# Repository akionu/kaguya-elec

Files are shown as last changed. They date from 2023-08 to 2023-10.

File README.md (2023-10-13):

# kaguya-elec

CanSatのための小型電装基板です。第19回能代宇宙イベント出場機体『かぐや』（同志社大学）のために作りました。

kiban

- 大幅な小型化を実現しました（当団体比）。42x25mmでここまでできる！
- 安定して動作しています。
- 50mから自由落下しても故障しませんでした（投下1回目）。

ブロック図：
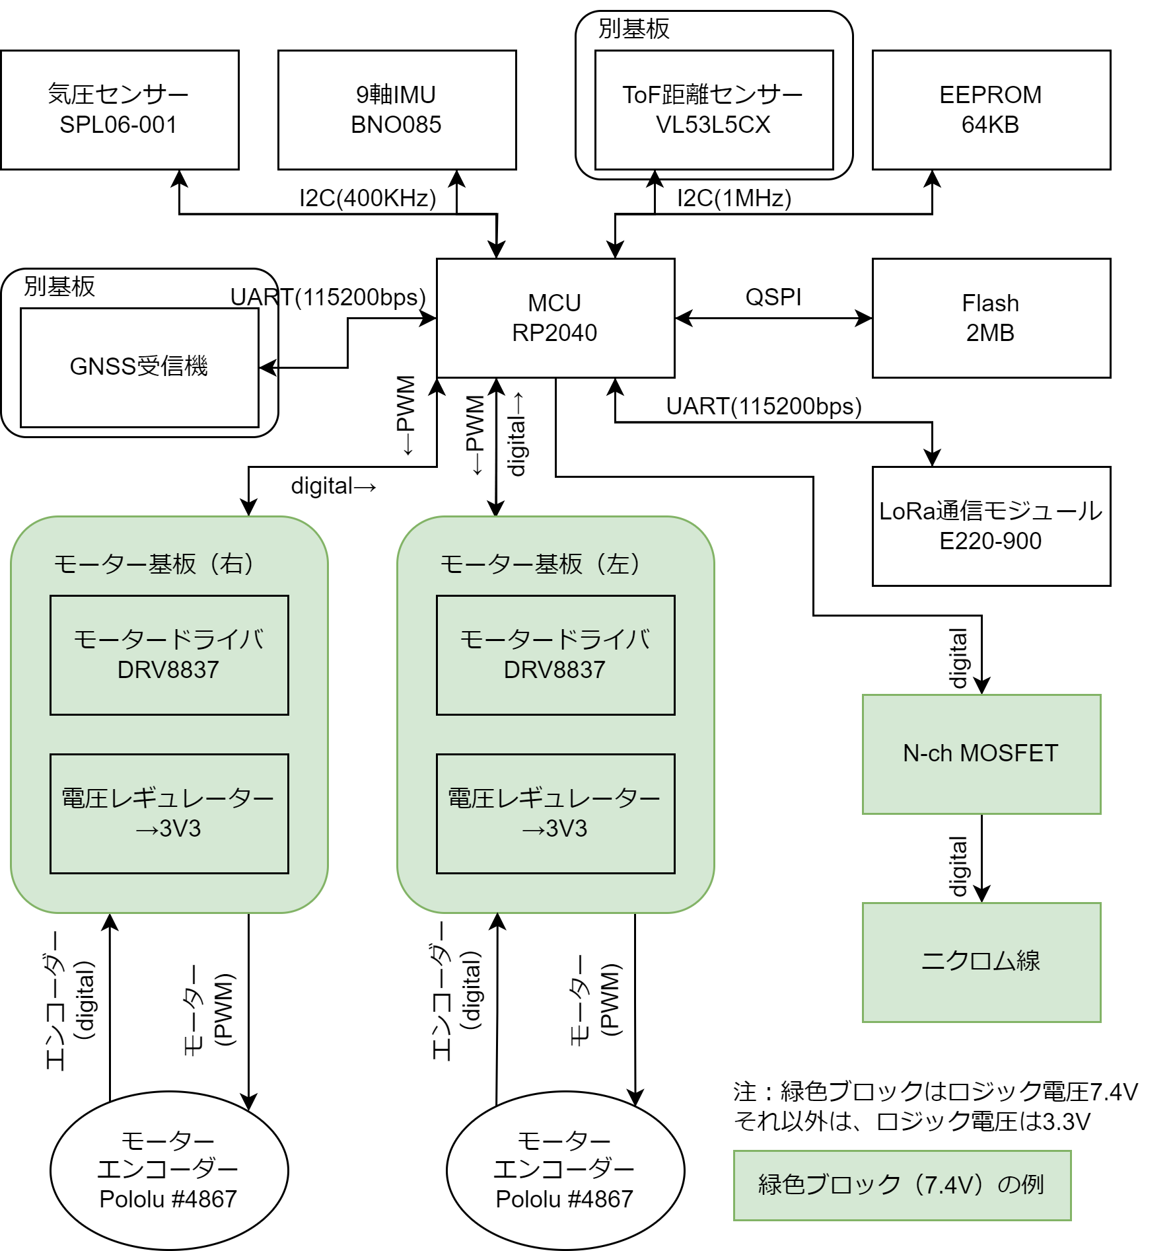
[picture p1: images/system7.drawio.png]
block_diagram

中身としては、RP2040を中心に、電源(DCDC)、無線（LoRa）、センサー（9軸IMU・気圧）、外付けセンサー用コネクタ（GPS・ToF測距）といった感じです。なお、モータードライバは別の基板として分離して使うようにしてあります。

回路図（詳しくはKiCadのデータを参照）：
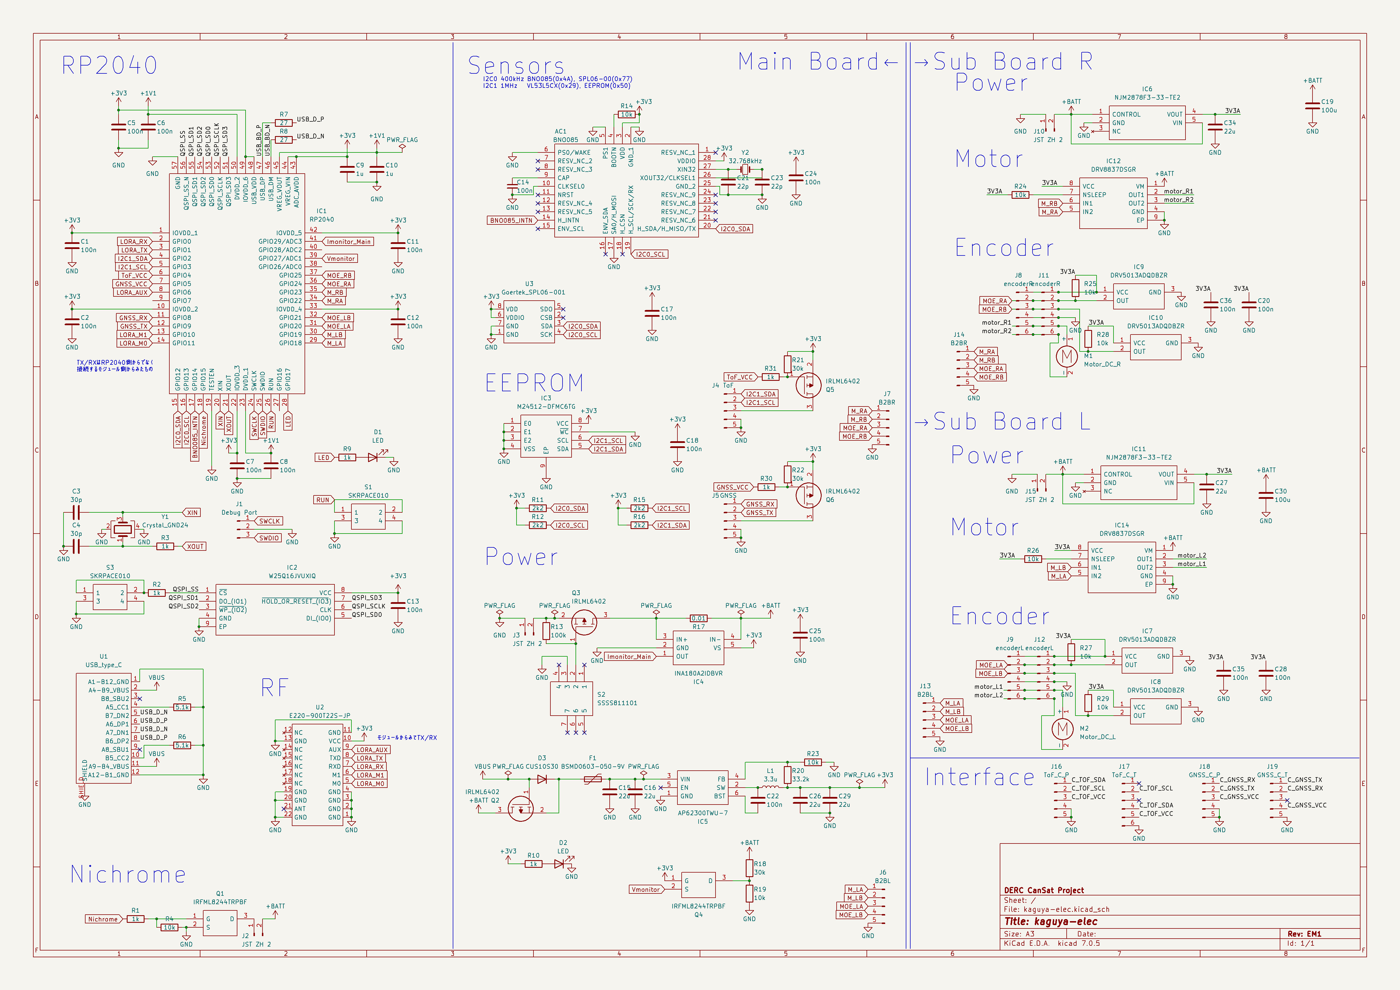
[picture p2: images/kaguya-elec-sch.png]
schematic


アートワーク：
表：
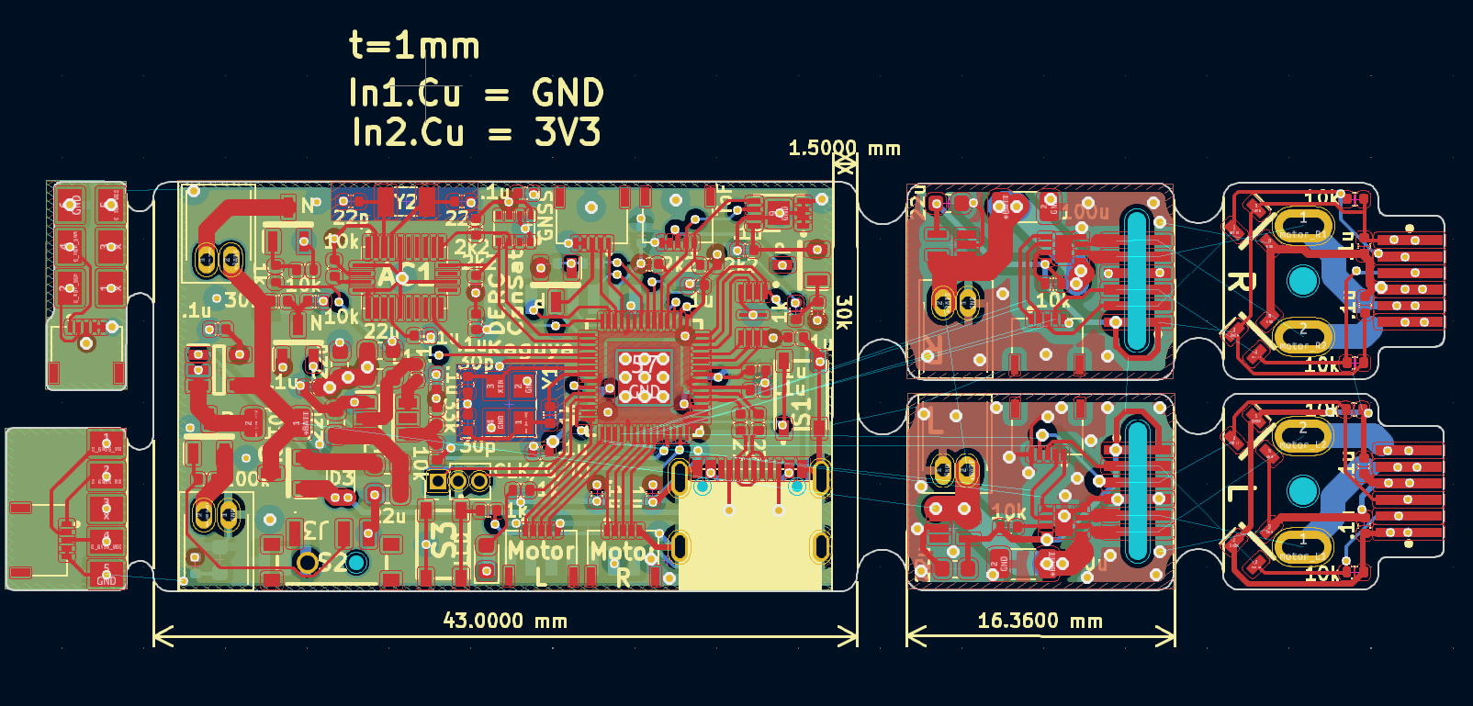
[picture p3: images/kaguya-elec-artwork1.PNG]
pcb_front

裏：
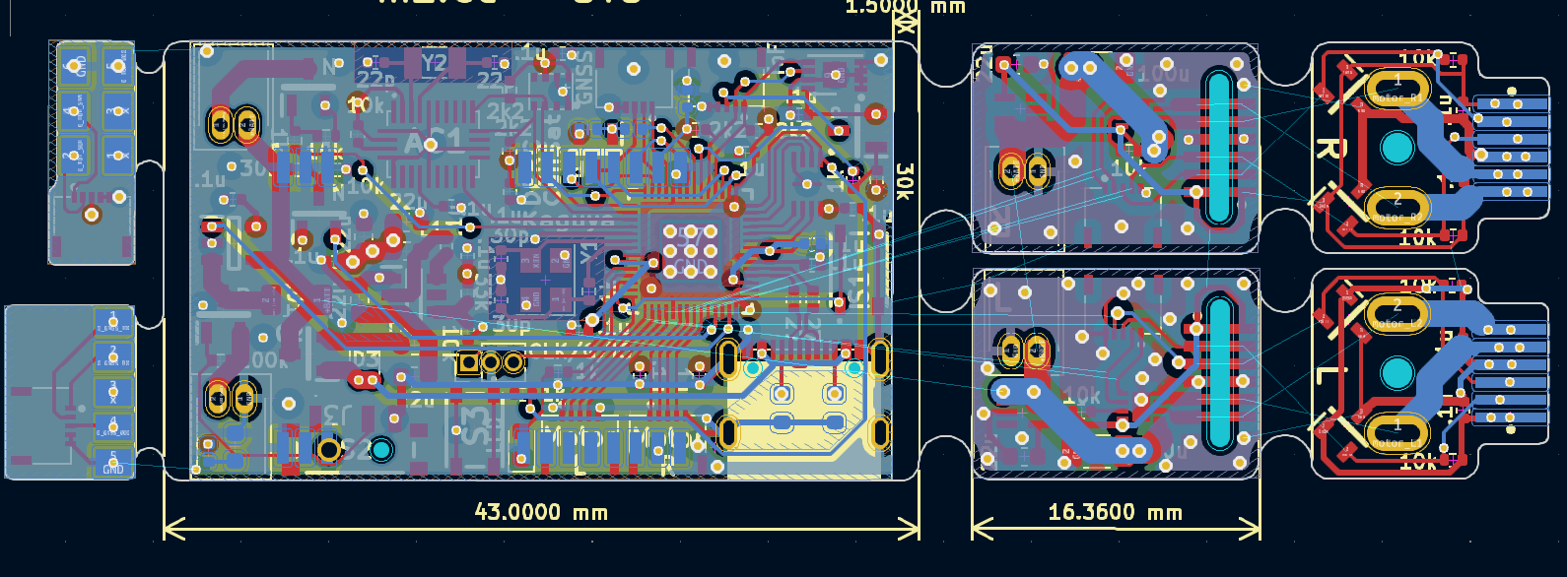
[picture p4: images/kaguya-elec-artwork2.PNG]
pcb_back


## 『かぐや』について

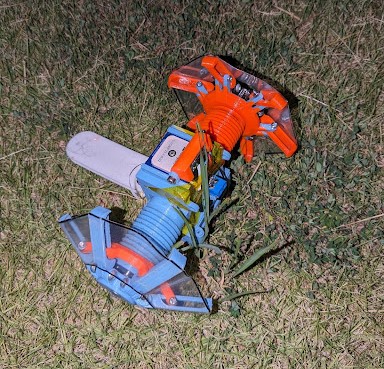
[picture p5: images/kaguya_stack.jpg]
kaguya_stack


第19回能代宇宙イベント出場機体『かぐや』（同志社大学）の基板です。
この機体の特徴：
- 成功率向上のため、2機体投下
    - タテに二つ重ねて投下するのでなく、制御性向上のため、ヨコに2つ並べてキャリアに収納
    - そのためのタイヤ展開
- 小型の基板

3回投下した中で、投下2回目の7mが最良の結果でした。実際の状況は大会報告書を参照されたいですが、走破性の不足によるスタックが一番の問題でした（3回ともプログラムは正常に動作・ログ取得）。
- 機体：運営特別賞
- ポスター：能代ロケット実験場　所長賞

なお、この基板で動かしたコードもGitHub上で公開しています。
[リンク](https://github.com/Yudetamago-AM/kaguya-code)

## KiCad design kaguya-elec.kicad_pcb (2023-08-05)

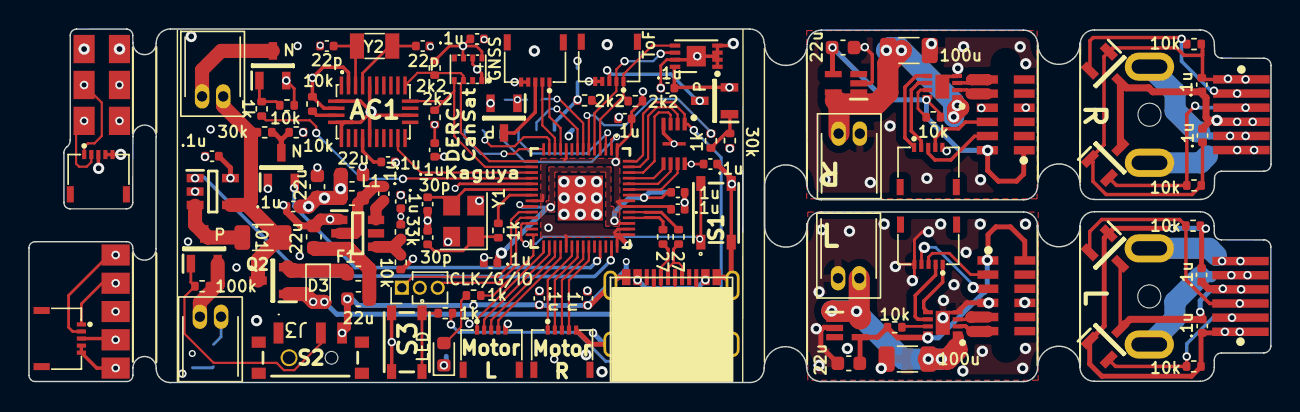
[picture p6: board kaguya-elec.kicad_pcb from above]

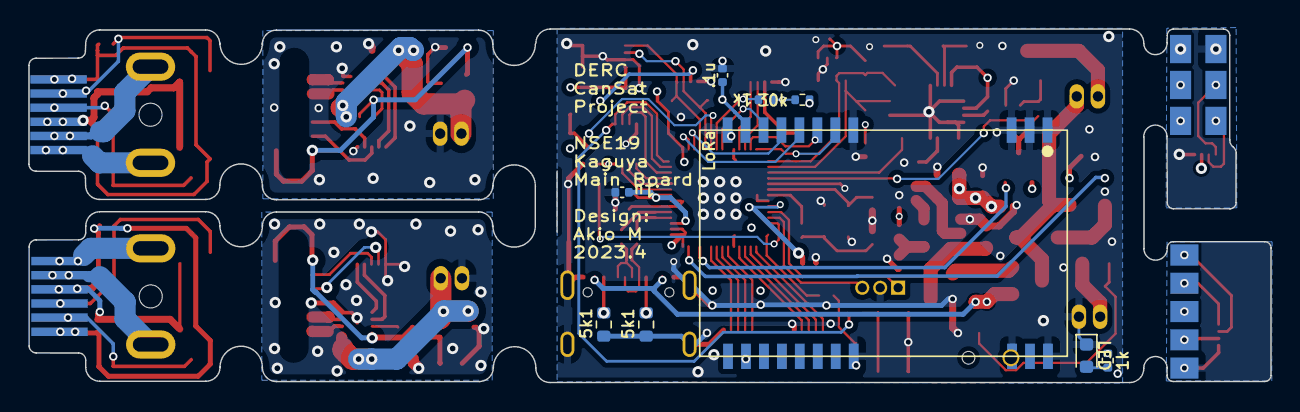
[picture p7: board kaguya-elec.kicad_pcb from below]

Board: 4 copper layers, 87.9 x 25.0 mm, 118 parts (9 on the bottom side), 84 nets.

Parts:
AC1: BNO085
C1, C2, C5, C6, C7, C8, C11, C12, C13, C14, C17, C18, C20, C22, C24, C25, C28, C35, C36: 100n; C_0402_1005Metric
C3, C4: 30p; C_0402_1005Metric
C9, C10: 1u; C_0402_1005Metric
C15, C16, C26, C27, C29, C34: 22u; C_0603_1608Metric
C19, C30: 100u; C_1206_3216Metric
C21, C23: 22p; C_0402_1005Metric
D1, D2: LED; LED_0603_1608Metric
D3: CUS10S30; D_SOD-323
F1: BSMD0603-050-9V; Fuse_0603_1608Metric
IC1: RP2040; RP2040TR7
IC2: W25Q16JVUXIQ; SON50P300X200X60-9N
IC3: M24512-DFMC6TG; DFN-8-1EP_3x2mm_P0.5mm_EP1.36x1.46mm
IC4: INA180A2IDBVR; SOT95P280X145-5N
IC5: AP62300TWU-7; SOT95P280X100-6N
IC6, IC11: NJM2878F3-33-TE2; SOT65P210X100-5N
IC7, IC8, IC9, IC10: DRV5013ADQDBZR; SOT95P237X112-3N
IC12, IC14: DRV8837DSGR; SON50P200X200X80-9N
J1: Debug Port; PinHeader_1x03_P1.27mm_Vertical
J2, J3, J10, J15: JST ZH 2; JST ZH 2 Side
J4: ToF; HC-FPC-05-10-5RLTAG
J5: GNSS; HC-FPC-05-10-5RLTAG
J6, J13: B2BL; HC-FPC-05-10-5RLTAG
J7, J14: B2BR; HC-FPC-05-10-5RLTAG
J8: encoderR; encoder connector p-side
J9: encoderL; encoder connector p-side
J11: encoderR; encoder connector e-side
J12: encoderL; encoder connector e-side
J16: ToF_C_P; HC-FPC-05-10-5RLTAG
J17: ToF_C_T; ToF_Flat2
J18: GNSS_C_P; HC-FPC-05-10-5RLTAG
J19: GNSS_C_T; GNSS_Flat
L1: 3.3u; L_0603_1608Metric
M1: Motor_DC_R; motor
M2: Motor_DC_L; motor
Q1, Q4: IRFML8244TRPBF; SOT95P237X112-3N
Q2, Q3, Q5, Q6: IRLML6402; SOT95P237X112-3N
R1, R2, R3, R9, R10, R30, R31: 1k; R_0402_1005Metric
R4, R14, R19, R23, R24, R25, R26, R27, R28, R29: 10k; R_0402_1005Metric
R5, R6: 5.1k; R_0603_1608Metric
R7, R8: 27; R_0402_1005Metric
R11, R12, R15, R16: 2k2; R_0402_1005Metric
R13: 100k; R_0402_1005Metric
R17: 0.01; R_1206_3216Metric
R18, R21, R22: 30k; R_0402_1005Metric
R20: 33.2k; R_0402_1005Metric
S1, S3: SKRPACE010; SMT_4.2X3.2_
S2: SSSS811101
U1: USB_type_C; USB_typeC_t
U2: E220-900T22S-JP; E220-900T22S JP
U3: Goertek_SPL06-001; Goertek SPL06-001
Y1: Crystal_GND24; Crystal_SMD_3225-4Pin_3.2x2.5mm
Y2: 32.768kHz; Crystal_SMD_3215-2Pin_3.2x1.5mm

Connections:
+1V1: C6.1, C8.1, C10.1, IC1.23 (DVDD_1), IC1.45 (VREG_VOUT), IC1.50 (DVDD_2)
+3V3: AC1.3 (VDD), AC1.28 (VDDIO), C1.1, C2.1, C5.1, C7.1, C9.1, C11.1, C12.1, C13.1, C17.1, C18.1, C24.1, C25.1, C26.1, C29.1, IC1.1 (IOVDD_1), IC1.10 (IOVDD_2), IC1.22 (IOVDD_3), IC1.33 (IOVDD_4), IC1.42 (IOVDD_5), IC1.43 (ADC_AVDD), IC1.44 (VREG_VIN), IC1.48 (USB_VDD), IC1.49 (IOVDD_6), IC2.8 (VCC), IC3.8 (VCC), IC4.5 (VS), L1.2, Q4.1 (G), Q5.2, Q6.2, R10.1, R11.1, R12.1, R14.2, R15.1, R16.1, R20.2, R21.1, R22.1, U2.10 (VCC), U3.6 (VDDIO), U3.8 (VDD)
+BATT: C19.1, C30.1, IC4.4 (IN-), IC6.1 (CONTROL), IC6.5 (VIN), IC11.1 (CONTROL), IC11.5 (VIN), IC12.1 (VM), IC14.1 (VM), J2.2, J10.2, J15.2, Q2.3, R17.1, R18.1
/3V3A: C20.1, C27.1, C28.1, C34.1, C35.1, C36.1, IC6.4 (VOUT), IC7.1 (VCC), IC8.1 (VCC), IC9.1 (VCC), IC10.1 (VCC), IC11.4 (VOUT), IC12.8 (VCC), IC14.8 (VCC), J8.1, J9.1, J11.1, J12.1, R24.1, R25.2, R26.1, R27.1, R28.2, R29.1
/C_GNSS_RX: J18.1, J19.2
/C_GNSS_TX: J18.2, J19.1
/C_GNSS_VCC: J18.3, J19.4
/C_TOF_SCL: J16.2, J17.2
/C_TOF_SDA: J16.1, J17.4
/C_TOF_VCC: J16.3, J17.5
/QSPI_SCLK: IC1.52 (QSPI_SCLK), IC2.6 (CLK)
/QSPI_SD0: IC1.53 (QSPI_SD0), IC2.5 (DI_(IO0))
/QSPI_SD1: IC1.55 (QSPI_SD1), IC2.2 (DO_(IO1))
/QSPI_SD2: IC1.54 (QSPI_SD2), IC2.3 (~WP_(IO2))
/QSPI_SD3: IC1.51 (QSPI_SD3), IC2.7 (~HOLD_OR_RESET_(IO3))
/QSPI_SS: IC1.56 (QSPI_SS_N), IC2.1 (~CS), R2.2
/USB_BD_N: IC1.46 (USB_DM), R8.1
/USB_BD_P: IC1.47 (USB_DP), R7.1
/USB_D_N: R8.2, U1.5 (B7_DN2), U1.7 (A7_DN1)
/USB_D_P: R7.2, U1.6 (A6_DP1), U1.8 (B6_DP2)
/motor_L1: IC14.3 (OUT2), J9.5, J12.5, M2.1 (+)
/motor_L2: IC14.2 (OUT1), J9.6, J12.6, M2.2 (-)
/motor_R1: IC12.2 (OUT1), J8.5, J11.5, M1.1 (+)
/motor_R2: IC12.3 (OUT2), J8.6, J11.6, M1.2 (-)
BNO085_INTN: AC1.14 (H_INTN), IC1.17 (GPIO14)
GND: AC1.2 (GND_1), AC1.5 (PS1), AC1.6 (PS0/WAKE), AC1.10 (CLKSEL0), AC1.17 (SA0/H_MOSI), AC1.25 (GND_2), C1.2, C2.2, C3.1, C4.1, C5.2, C6.2, C7.2, C8.2, C9.2, C10.2, C11.2, C12.2, C13.2, C14.2, C15.2, C16.2, C17.2, C18.2, C19.2, C20.2, C21.2, C23.2, C24.2, C25.2, C26.2, C27.2, C28.2, C29.2, C30.2, C34.2, C35.2, C36.2, D1.1 (K), D2.1 (K), IC1.19 (TESTEN), IC1.57 (GND), IC2.4 (GND), IC2.9 (EP), IC3.1 (E0), IC3.2 (E1), IC3.3 (E2), IC3.4 (VSS), IC3.7 (~WC), IC3.9 (EP), IC4.2 (GND), IC5.1 (GND), IC6.2 (GND), IC7.3 (GND), IC8.3 (GND), IC9.3 (GND), IC10.3 (GND), IC11.2 (GND), IC12.4 (GND), IC12.9 (EP), IC14.4 (GND), IC14.9 (EP), J1.2, J3.1, J4.4, J4.5, J5.4, J5.5, J6.5, J7.5, J8.4, J9.4, J10.1, J11.4, J12.4, J13.5, J14.5, J15.1, J16.4, J16.5, J17.6, J18.4, J18.5, J19.5, Q1.2 (S), R4.2, R5.2, R6.2, R19.2, R23.1, S1.3, S1.4, S2.3, S3.3, S3.4, U1.1 (A1-B12_GND), U1.12 (A12-B1_GND), U1.SHIELD, U2.1 (GND), U2.2 (GND), U2.3 (GND), U2.4 (GND), U2.11 (GND), U2.13 (GND), U2.19 (GND), U2.20 (GND), U2.22 (GND), U3.1 (GND), U3.7 (GND), Y1.2, Y1.4
GNSS_RX: IC1.11 (GPIO8), J5.1
GNSS_TX: IC1.12 (GPIO9), J5.2
GNSS_VCC: IC1.7 (GPIO5), R30.1
I2C0_SCL: AC1.19 (H_SCL/SCK/RX), IC1.16 (GPIO13), R12.2, U3.4 (SCK)
I2C0_SDA: AC1.20 (H_SDA/H_MISO/TX), IC1.15 (GPIO12), R11.2, U3.3 (SDA)
I2C1_SCL: IC1.5 (GPIO3), IC3.6 (SCL), J4.2, R15.2
I2C1_SDA: IC1.4 (GPIO2), IC3.5 (SDA), J4.1, R16.2
Imonitor_Main: IC1.41 (GPIO29/ADC3), IC4.1 (OUT)
LED: IC1.28 (GPIO17), R9.1
LORA_AUX: IC1.8 (GPIO6), U2.9 (AUX)
LORA_M0: IC1.14 (GPIO11), U2.5 (M0)
LORA_M1: IC1.13 (GPIO10), U2.6 (M1)
LORA_RX: IC1.2 (GPIO0), U2.7 (RXD)
LORA_TX: IC1.3 (GPIO1), U2.8 (TXD)
MOE_LA: IC1.31 (GPIO20), IC7.2 (OUT), J6.3, J9.2, J12.2, J13.3, R27.2
MOE_LB: IC1.32 (GPIO21), IC8.2 (OUT), J6.4, J9.3, J12.3, J13.4, R29.2
MOE_RA: IC1.36 (GPIO24), IC9.2 (OUT), J7.3, J8.2, J11.2, J14.3, R25.1
MOE_RB: IC1.37 (GPIO25), IC10.2 (OUT), J7.4, J8.3, J11.3, J14.4, R28.1
M_LA: IC1.29 (GPIO18), IC14.5 (IN2), J6.1, J13.1
M_LB: IC1.30 (GPIO19), IC14.6 (IN1), J6.2, J13.2
M_RA: IC1.34 (GPIO22), IC12.5 (IN2), J7.1, J14.1
M_RB: IC1.35 (GPIO23), IC12.6 (IN1), J7.2, J14.2
unnamed: AC1.4 (BOOTN), R14.1
unnamed: AC1.9 (CAP), C14.1
unnamed: AC1.26 (XOUT32/CLKSEL1), C23.1, Y2.2
unnamed: AC1.27 (XIN32), C21.1, Y2.1
unnamed: C4.2, R3.1, Y1.1
unnamed: C15.1, C16.1, F1.2, IC5.3 (VIN)
unnamed: C22.1, IC5.2 (SW), L1.1
unnamed: C22.2, IC5.6 (BST)
unnamed: D1.2 (A), R9.2
unnamed: D2.2 (A), R10.2
unnamed: D3.1 (K), F1.1, Q2.2
unnamed: IC4.3 (IN+), Q3.3, R17.2
unnamed: IC5.4 (FB), R20.1, R23.2
unnamed: IC12.7 (NSLEEP), R24.2
unnamed: IC14.7 (NSLEEP), R26.2
unnamed: J2.1, Q1.3 (D)
unnamed: J3.2, Q3.2, R13.1
unnamed: J4.3, Q5.3
unnamed: J5.3, Q6.3
unnamed: Q1.1 (G), R1.2, R4.1
unnamed: Q3.1, R13.2, S2.2
unnamed: Q4.3 (D), R18.2, R19.1
unnamed: Q5.1, R21.2, R31.2
unnamed: Q6.1, R22.2, R30.2
unnamed: R2.1, S3.1, S3.2
unnamed: R5.1, U1.4 (A5_CC1)
unnamed: R6.1, U1.10 (B5_CC2)
Nichrome: IC1.18 (GPIO15), R1.1
RUN: IC1.26 (RUN), S1.1, S1.2
SWCLK: IC1.24 (SWCLK), J1.1
SWDIO: IC1.25 (SWDIO), J1.3
ToF_VCC: IC1.6 (GPIO4), R31.1
VBUS: D3.2 (A), Q2.1, U1.2 (A4-B9_VBUS), U1.11 (A9-B4_VBUS)
Vmonitor: IC1.39 (GPIO27/ADC1), Q4.2 (S)
XIN: C3.2, IC1.20 (XIN), Y1.3
XOUT: IC1.21 (XOUT), R3.2

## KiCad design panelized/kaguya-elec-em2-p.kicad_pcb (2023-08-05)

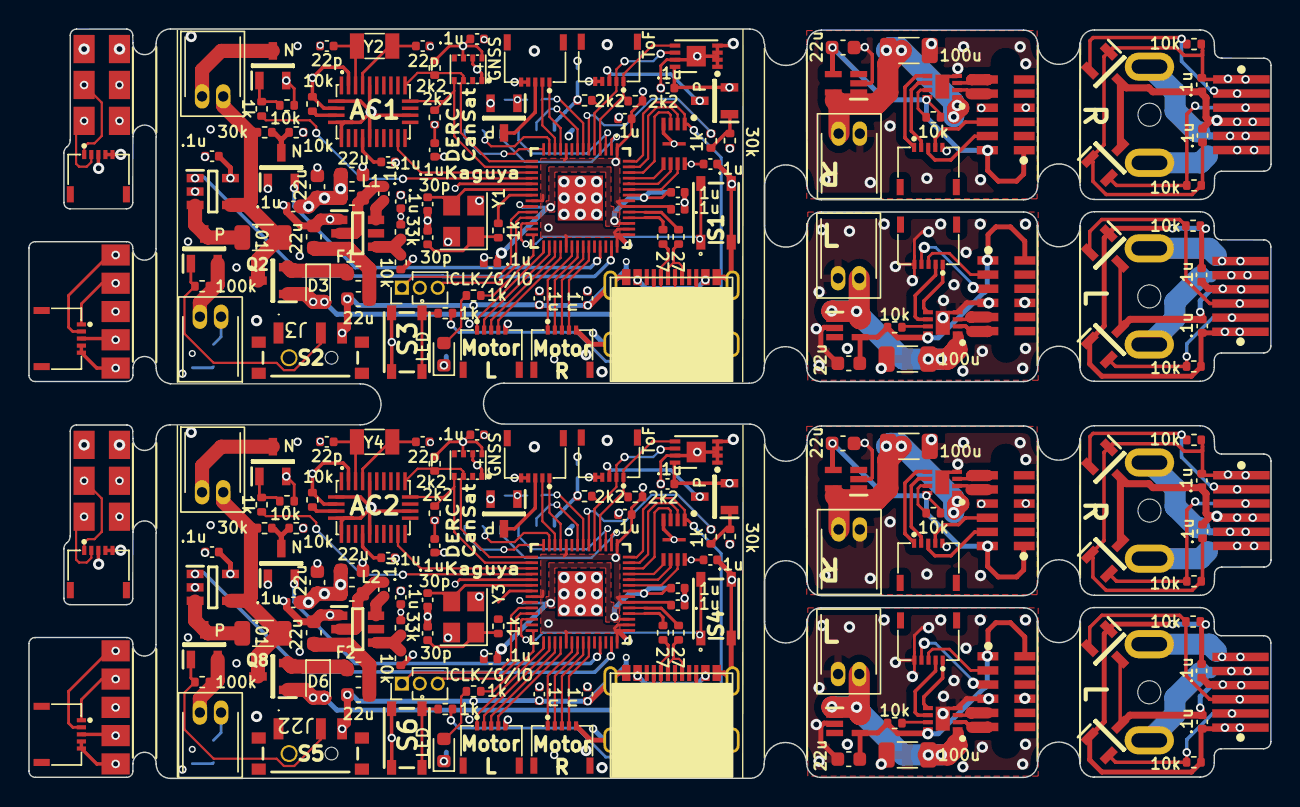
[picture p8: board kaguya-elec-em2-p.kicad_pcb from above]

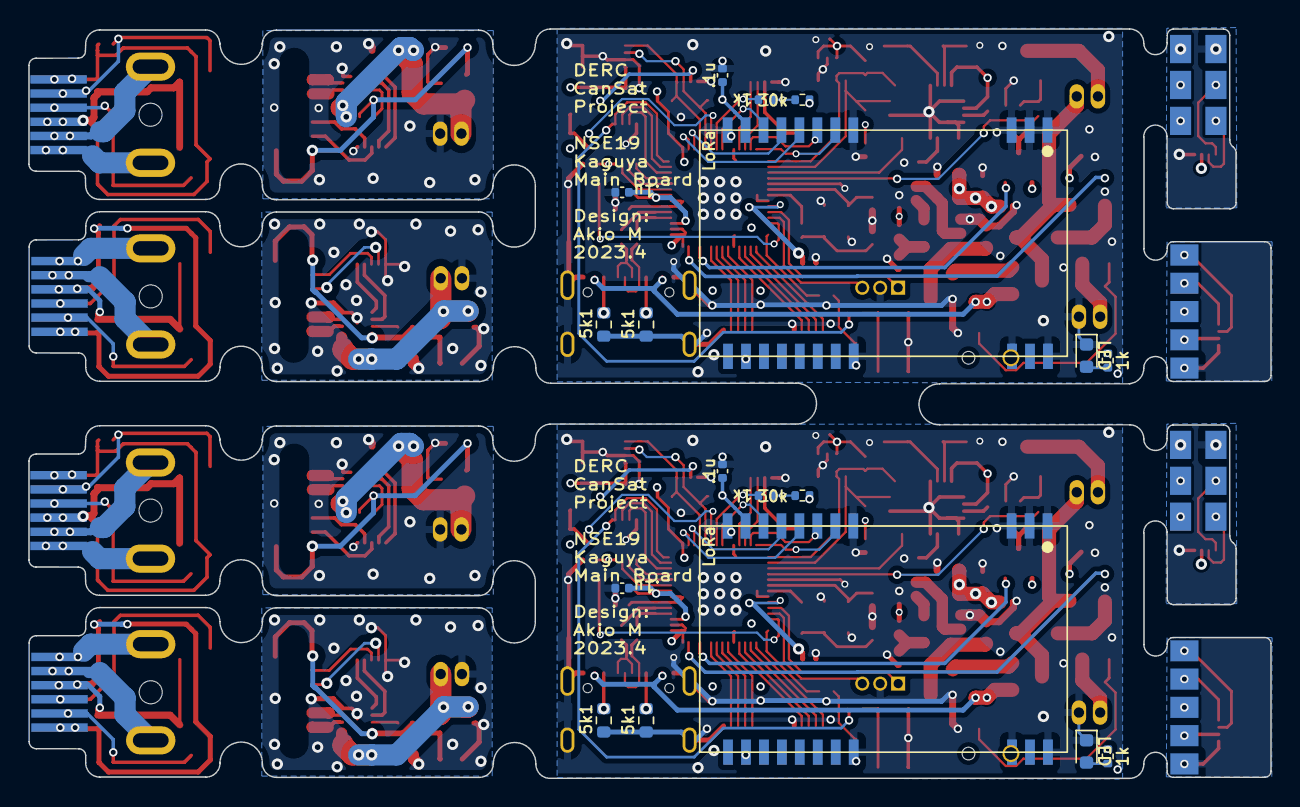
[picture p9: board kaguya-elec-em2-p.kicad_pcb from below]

Board: 4 copper layers, 87.9 x 53.0 mm, 236 parts (18 on the bottom side), 84 nets.

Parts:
AC1, AC2: BNO085
C1, C2, C5, C6, C7, C8, C11, C12, C13, C14, C17, C18, C20, C22, C24, C25, C28, C31, C32, C35, C36, C38, C39, C40, C41, C44, C45, C46, C47, C50, C51, C53, C55, C57, C58, C61, C65, C66: 100n; C_0402_1005Metric
C3, C4, C33, C37: 30p; C_0402_1005Metric
C9, C10, C42, C43: 1u; C_0402_1005Metric
C15, C16, C26, C27, C29, C34, C48, C49, C59, C60, C62, C64: 22u; C_0603_1608Metric
C19, C30, C52, C63: 100u; C_1206_3216Metric
C21, C23, C54, C56: 22p; C_0402_1005Metric
D1, D2, D4, D5: LED; LED_0603_1608Metric
D3, D6: CUS10S30; D_SOD-323
F1, F2: BSMD0603-050-9V; Fuse_0603_1608Metric
IC1, IC13: RP2040; RP2040TR7
IC2, IC15: W25Q16JVUXIQ; SON50P300X200X60-9N
IC3, IC16: M24512-DFMC6TG; DFN-8-1EP_3x2mm_P0.5mm_EP1.36x1.46mm
IC4, IC17: INA180A2IDBVR; SOT95P280X145-5N
IC5, IC18: AP62300TWU-7; SOT95P280X100-6N
IC6, IC11, IC19, IC24: NJM2878F3-33-TE2; SOT65P210X100-5N
IC7, IC8, IC9, IC10, IC20, IC21, IC22, IC23: DRV5013ADQDBZR; SOT95P237X112-3N
IC12, IC14, IC25, IC26: DRV8837DSGR; SON50P200X200X80-9N
J1, J20: Debug Port; PinHeader_1x03_P1.27mm_Vertical
J2, J3, J10, J15, J21, J22, J29, J34: JST ZH 2; JST ZH 2 Side
J4, J23: ToF; HC-FPC-05-10-5RLTAG
J5, J24: GNSS; HC-FPC-05-10-5RLTAG
J6, J13, J25, J32: B2BL; HC-FPC-05-10-5RLTAG
J7, J14, J26, J33: B2BR; HC-FPC-05-10-5RLTAG
J8, J27: encoderR; encoder connector p-side
J9, J28: encoderL; encoder connector p-side
J11, J30: encoderR; encoder connector e-side
J12, J31: encoderL; encoder connector e-side
J16, J35: ToF_C_P; HC-FPC-05-10-5RLTAG
J17, J36: ToF_C_T; ToF_Flat2
J18, J37: GNSS_C_P; HC-FPC-05-10-5RLTAG
J19, J38: GNSS_C_T; GNSS_Flat
L1, L2: 3.3u; L_0603_1608Metric
M1, M3: Motor_DC_R; motor
M2, M4: Motor_DC_L; motor
Q1, Q4, Q7, Q10: IRFML8244TRPBF; SOT95P237X112-3N
Q2, Q3, Q5, Q6, Q8, Q9, Q11, Q12: IRLML6402; SOT95P237X112-3N
R1, R2, R3, R9, R10, R30, R31, R32, R33, R34, R40, R41, R61, R62: 1k; R_0402_1005Metric
R4, R14, R19, R23, R24, R25, R26, R27, R28, R29, R35, R45, R50, R54, R55, R56, R57, R58, R59, R60: 10k; R_0402_1005Metric
R5, R6, R36, R37: 5.1k; R_0603_1608Metric
R7, R8, R38, R39: 27; R_0402_1005Metric
R11, R12, R15, R16, R42, R43, R46, R47: 2k2; R_0402_1005Metric
R13, R44: 100k; R_0402_1005Metric
R17, R48: 0.01; R_1206_3216Metric
R18, R21, R22, R49, R52, R53: 30k; R_0402_1005Metric
R20, R51: 33.2k; R_0402_1005Metric
S1, S3, S4, S6: SKRPACE010; SMT_4.2X3.2_
S2, S5: SSSS811101
U1, U4: USB_type_C; USB_typeC_t
U2, U5: E220-900T22S-JP; E220-900T22S JP
U3, U6: Goertek_SPL06-001; Goertek SPL06-001
Y1, Y3: Crystal_GND24; Crystal_SMD_3225-4Pin_3.2x2.5mm
Y2, Y4: 32.768kHz; Crystal_SMD_3215-2Pin_3.2x1.5mm

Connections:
+1V1: C6.1, C8.1, C10.1, C39.1, C41.1, C43.1, IC1.23 (DVDD_1), IC1.45 (VREG_VOUT), IC1.50 (DVDD_2), IC13.23 (DVDD_1), IC13.45 (VREG_VOUT), IC13.50 (DVDD_2)
+3V3: AC1.3 (VDD), AC1.28 (VDDIO), AC2.3 (VDD), AC2.28 (VDDIO), C1.1, C2.1, C5.1, C7.1, C9.1, C11.1, C12.1, C13.1, C17.1, C18.1, C24.1, C25.1, C26.1, C29.1, C31.1, C32.1, C38.1, C40.1, C42.1, C44.1, C45.1, C46.1, C50.1, C51.1, C57.1, C58.1, C59.1, C62.1, IC1.1 (IOVDD_1), IC1.10 (IOVDD_2), IC1.22 (IOVDD_3), IC1.33 (IOVDD_4), IC1.42 (IOVDD_5), IC1.43 (ADC_AVDD), IC1.44 (VREG_VIN), IC1.48 (USB_VDD), IC1.49 (IOVDD_6), IC2.8 (VCC), IC3.8 (VCC), IC4.5 (VS), IC13.1 (IOVDD_1), IC13.10 (IOVDD_2), IC13.22 (IOVDD_3), IC13.33 (IOVDD_4), IC13.42 (IOVDD_5), IC13.43 (ADC_AVDD), IC13.44 (VREG_VIN), IC13.48 (USB_VDD), IC13.49 (IOVDD_6), IC15.8 (VCC), IC16.8 (VCC), IC17.5 (VS), L1.2, L2.2, Q4.1 (G), Q5.2, Q6.2, Q10.1 (G), Q11.2, Q12.2, R10.1, R11.1, R12.1, R14.2, R15.1, R16.1, R20.2, R21.1, R22.1, R41.1, R42.1, R43.1, R45.2, R46.1, R47.1, R51.2, R52.1, R53.1, U2.10 (VCC), U3.6 (VDDIO), U3.8 (VDD), U5.10 (VCC), U6.6 (VDDIO), U6.8 (VDD)
+BATT: C19.1, C30.1, C52.1, C63.1, IC4.4 (IN-), IC6.1 (CONTROL), IC6.5 (VIN), IC11.1 (CONTROL), IC11.5 (VIN), IC12.1 (VM), IC14.1 (VM), IC17.4 (IN-), IC19.1 (CONTROL), IC19.5 (VIN), IC24.1 (CONTROL), IC24.5 (VIN), IC25.1 (VM), IC26.1 (VM), J2.2, J10.2, J15.2, J21.2, J29.2, J34.2, Q2.3, Q8.3, R17.1, R18.1, R48.1, R49.1
/3V3A: C20.1, C27.1, C28.1, C34.1, C35.1, C36.1, C53.1, C60.1, C61.1, C64.1, C65.1, C66.1, IC6.4 (VOUT), IC7.1 (VCC), IC8.1 (VCC), IC9.1 (VCC), IC10.1 (VCC), IC11.4 (VOUT), IC12.8 (VCC), IC14.8 (VCC), IC19.4 (VOUT), IC20.1 (VCC), IC21.1 (VCC), IC22.1 (VCC), IC23.1 (VCC), IC24.4 (VOUT), IC25.8 (VCC), IC26.8 (VCC), J8.1, J9.1, J11.1, J12.1, J27.1, J28.1, J30.1, J31.1, R24.1, R25.2, R26.1, R27.1, R28.2, R29.1, R55.1, R56.2, R57.1, R58.1, R59.2, R60.1
/C_GNSS_RX: J18.1, J19.2, J37.1, J38.2
/C_GNSS_TX: J18.2, J19.1, J37.2, J38.1
/C_GNSS_VCC: J18.3, J19.4, J37.3, J38.4
/C_TOF_SCL: J16.2, J17.2, J35.2, J36.2
/C_TOF_SDA: J16.1, J17.4, J35.1, J36.4
/C_TOF_VCC: J16.3, J17.5, J35.3, J36.5
/QSPI_SCLK: IC1.52 (QSPI_SCLK), IC2.6 (CLK), IC13.52 (QSPI_SCLK), IC15.6 (CLK)
/QSPI_SD0: IC1.53 (QSPI_SD0), IC2.5 (DI_(IO0)), IC13.53 (QSPI_SD0), IC15.5 (DI_(IO0))
/QSPI_SD1: IC1.55 (QSPI_SD1), IC2.2 (DO_(IO1)), IC13.55 (QSPI_SD1), IC15.2 (DO_(IO1))
/QSPI_SD2: IC1.54 (QSPI_SD2), IC2.3 (~WP_(IO2)), IC13.54 (QSPI_SD2), IC15.3 (~WP_(IO2))
/QSPI_SD3: IC1.51 (QSPI_SD3), IC2.7 (~HOLD_OR_RESET_(IO3)), IC13.51 (QSPI_SD3), IC15.7 (~HOLD_OR_RESET_(IO3))
/QSPI_SS: IC1.56 (QSPI_SS_N), IC2.1 (~CS), IC13.56 (QSPI_SS_N), IC15.1 (~CS), R2.2, R33.2
/USB_BD_N: IC1.46 (USB_DM), IC13.46 (USB_DM), R8.1, R39.1
/USB_BD_P: IC1.47 (USB_DP), IC13.47 (USB_DP), R7.1, R38.1
/USB_D_N: R8.2, R39.2, U1.5 (B7_DN2), U1.7 (A7_DN1), U4.5 (B7_DN2), U4.7 (A7_DN1)
/USB_D_P: R7.2, R38.2, U1.6 (A6_DP1), U1.8 (B6_DP2), U4.6 (A6_DP1), U4.8 (B6_DP2)
/motor_L1: IC14.3 (OUT2), IC26.3 (OUT2), J9.5, J12.5, J28.5, J31.5, M2.1 (+), M4.1 (+)
/motor_L2: IC14.2 (OUT1), IC26.2 (OUT1), J9.6, J12.6, J28.6, J31.6, M2.2 (-), M4.2 (-)
/motor_R1: IC12.2 (OUT1), IC25.2 (OUT1), J8.5, J11.5, J27.5, J30.5, M1.1 (+), M3.1 (+)
/motor_R2: IC12.3 (OUT2), IC25.3 (OUT2), J8.6, J11.6, J27.6, J30.6, M1.2 (-), M3.2 (-)
BNO085_INTN: AC1.14 (H_INTN), AC2.14 (H_INTN), IC1.17 (GPIO14), IC13.17 (GPIO14)
GND: AC1.2 (GND_1), AC1.5 (PS1), AC1.6 (PS0/WAKE), AC1.10 (CLKSEL0), AC1.17 (SA0/H_MOSI), AC1.25 (GND_2), AC2.2 (GND_1), AC2.5 (PS1), AC2.6 (PS0/WAKE), AC2.10 (CLKSEL0), AC2.17 (SA0/H_MOSI), AC2.25 (GND_2), C1.2, C2.2, C3.1, C4.1, C5.2, C6.2, C7.2, C8.2, C9.2, C10.2, C11.2, C12.2, C13.2, C14.2, C15.2, C16.2, C17.2, C18.2, C19.2, C20.2, C21.2, C23.2, C24.2, C25.2, C26.2, C27.2, C28.2, C29.2, C30.2, C31.2, C32.2, C33.1, C34.2, C35.2, C36.2, C37.1, C38.2, C39.2, C40.2, C41.2, C42.2, C43.2, C44.2, C45.2, C46.2, C47.2, C48.2, C49.2, C50.2, C51.2, C52.2, C53.2, C54.2, C56.2, C57.2, C58.2, C59.2, C60.2, C61.2, C62.2, C63.2, C64.2, C65.2, C66.2, D1.1 (K), D2.1 (K), D4.1 (K), D5.1 (K), IC1.19 (TESTEN), IC1.57 (GND), IC2.4 (GND), IC2.9 (EP), IC3.1 (E0), IC3.2 (E1), IC3.3 (E2), IC3.4 (VSS), IC3.7 (~WC), IC3.9 (EP), IC4.2 (GND), IC5.1 (GND), IC6.2 (GND), IC7.3 (GND), IC8.3 (GND), IC9.3 (GND), IC10.3 (GND), IC11.2 (GND), IC12.4 (GND), IC12.9 (EP), IC13.19 (TESTEN), IC13.57 (GND), IC14.4 (GND), IC14.9 (EP), IC15.4 (GND), IC15.9 (EP), IC16.1 (E0), IC16.2 (E1), IC16.3 (E2), IC16.4 (VSS), IC16.7 (~WC), IC16.9 (EP), IC17.2 (GND), IC18.1 (GND), IC19.2 (GND), IC20.3 (GND), IC21.3 (GND), IC22.3 (GND), IC23.3 (GND), IC24.2 (GND), IC25.4 (GND), IC25.9 (EP), IC26.4 (GND), IC26.9 (EP), J1.2, J3.1, J4.4, J4.5, J5.4, J5.5, J6.5, J7.5, J8.4, J9.4, J10.1, J11.4, J12.4, J13.5, J14.5, J15.1, J16.4, J16.5, J17.6, J18.4, J18.5, J19.5, J20.2, J22.1, J23.4, J23.5, J24.4, J24.5, J25.5, J26.5, J27.4, J28.4, J29.1, J30.4, J31.4, J32.5, J33.5, J34.1, J35.4, J35.5, J36.6, J37.4, J37.5, J38.5, Q1.2 (S), Q7.2 (S), R4.2, R5.2, R6.2, R19.2, R23.1, R35.2, R36.2, R37.2, R50.2, R54.1, S1.3, S1.4, S2.3, S3.3, S3.4, S4.3, S4.4, S5.3, S6.3, S6.4, U1.1 (A1-B12_GND), U1.12 (A12-B1_GND), U1.SHIELD, U2.1 (GND), U2.2 (GND), U2.3 (GND), U2.4 (GND), U2.11 (GND), U2.13 (GND), U2.19 (GND), U2.20 (GND), U2.22 (GND), U3.1 (GND), U3.7 (GND), U4.1 (A1-B12_GND), U4.12 (A12-B1_GND), U4.SHIELD, U5.1 (GND), U5.2 (GND), U5.3 (GND), U5.4 (GND), U5.11 (GND), U5.13 (GND), U5.19 (GND), U5.20 (GND), U5.22 (GND), U6.1 (GND), U6.7 (GND), Y1.2, Y1.4, Y3.2, Y3.4
GNSS_RX: IC1.11 (GPIO8), IC13.11 (GPIO8), J5.1, J24.1
GNSS_TX: IC1.12 (GPIO9), IC13.12 (GPIO9), J5.2, J24.2
GNSS_VCC: IC1.7 (GPIO5), IC13.7 (GPIO5), R30.1, R61.1
I2C0_SCL: AC1.19 (H_SCL/SCK/RX), AC2.19 (H_SCL/SCK/RX), IC1.16 (GPIO13), IC13.16 (GPIO13), R12.2, R43.2, U3.4 (SCK), U6.4 (SCK)
I2C0_SDA: AC1.20 (H_SDA/H_MISO/TX), AC2.20 (H_SDA/H_MISO/TX), IC1.15 (GPIO12), IC13.15 (GPIO12), R11.2, R42.2, U3.3 (SDA), U6.3 (SDA)
I2C1_SCL: IC1.5 (GPIO3), IC3.6 (SCL), IC13.5 (GPIO3), IC16.6 (SCL), J4.2, J23.2, R15.2, R46.2
I2C1_SDA: IC1.4 (GPIO2), IC3.5 (SDA), IC13.4 (GPIO2), IC16.5 (SDA), J4.1, J23.1, R16.2, R47.2
Imonitor_Main: IC1.41 (GPIO29/ADC3), IC4.1 (OUT), IC13.41 (GPIO29/ADC3), IC17.1 (OUT)
LED: IC1.28 (GPIO17), IC13.28 (GPIO17), R9.1, R40.1
LORA_AUX: IC1.8 (GPIO6), IC13.8 (GPIO6), U2.9 (AUX), U5.9 (AUX)
LORA_M0: IC1.14 (GPIO11), IC13.14 (GPIO11), U2.5 (M0), U5.5 (M0)
LORA_M1: IC1.13 (GPIO10), IC13.13 (GPIO10), U2.6 (M1), U5.6 (M1)
LORA_RX: IC1.2 (GPIO0), IC13.2 (GPIO0), U2.7 (RXD), U5.7 (RXD)
LORA_TX: IC1.3 (GPIO1), IC13.3 (GPIO1), U2.8 (TXD), U5.8 (TXD)
MOE_LA: IC1.31 (GPIO20), IC7.2 (OUT), IC13.31 (GPIO20), IC20.2 (OUT), J6.3, J9.2, J12.2, J13.3, J25.3, J28.2, J31.2, J32.3, R27.2, R58.2
MOE_LB: IC1.32 (GPIO21), IC8.2 (OUT), IC13.32 (GPIO21), IC21.2 (OUT), J6.4, J9.3, J12.3, J13.4, J25.4, J28.3, J31.3, J32.4, R29.2, R60.2
MOE_RA: IC1.36 (GPIO24), IC9.2 (OUT), IC13.36 (GPIO24), IC22.2 (OUT), J7.3, J8.2, J11.2, J14.3, J26.3, J27.2, J30.2, J33.3, R25.1, R56.1
MOE_RB: IC1.37 (GPIO25), IC10.2 (OUT), IC13.37 (GPIO25), IC23.2 (OUT), J7.4, J8.3, J11.3, J14.4, J26.4, J27.3, J30.3, J33.4, R28.1, R59.1
M_LA: IC1.29 (GPIO18), IC13.29 (GPIO18), IC14.5 (IN2), IC26.5 (IN2), J6.1, J13.1, J25.1, J32.1
M_LB: IC1.30 (GPIO19), IC13.30 (GPIO19), IC14.6 (IN1), IC26.6 (IN1), J6.2, J13.2, J25.2, J32.2
M_RA: IC1.34 (GPIO22), IC12.5 (IN2), IC13.34 (GPIO22), IC25.5 (IN2), J7.1, J14.1, J26.1, J33.1
M_RB: IC1.35 (GPIO23), IC12.6 (IN1), IC13.35 (GPIO23), IC25.6 (IN1), J7.2, J14.2, J26.2, J33.2
unnamed: AC1.4 (BOOTN), AC2.4 (BOOTN), R14.1, R45.1
unnamed: AC1.9 (CAP), AC2.9 (CAP), C14.1, C47.1
unnamed: AC1.26 (XOUT32/CLKSEL1), AC2.26 (XOUT32/CLKSEL1), C23.1, C56.1, Y2.2, Y4.2
unnamed: AC1.27 (XIN32), AC2.27 (XIN32), C21.1, C54.1, Y2.1, Y4.1
unnamed: C4.2, C37.2, R3.1, R34.1, Y1.1, Y3.1
unnamed: C15.1, C16.1, C48.1, C49.1, F1.2, F2.2, IC5.3 (VIN), IC18.3 (VIN)
unnamed: C22.1, C55.1, IC5.2 (SW), IC18.2 (SW), L1.1, L2.1
unnamed: C22.2, C55.2, IC5.6 (BST), IC18.6 (BST)
unnamed: D1.2 (A), D4.2 (A), R9.2, R40.2
unnamed: D2.2 (A), D5.2 (A), R10.2, R41.2
unnamed: D3.1 (K), D6.1 (K), F1.1, F2.1, Q2.2, Q8.2
unnamed: IC4.3 (IN+), IC17.3 (IN+), Q3.3, Q9.3, R17.2, R48.2
unnamed: IC5.4 (FB), IC18.4 (FB), R20.1, R23.2, R51.1, R54.2
unnamed: IC12.7 (NSLEEP), IC25.7 (NSLEEP), R24.2, R55.2
unnamed: IC14.7 (NSLEEP), IC26.7 (NSLEEP), R26.2, R57.2
unnamed: J2.1, J21.1, Q1.3 (D), Q7.3 (D)
unnamed: J3.2, J22.2, Q3.2, Q9.2, R13.1, R44.1
unnamed: J4.3, J23.3, Q5.3, Q11.3
unnamed: J5.3, J24.3, Q6.3, Q12.3
unnamed: Q1.1 (G), Q7.1 (G), R1.2, R4.1, R32.2, R35.1
unnamed: Q3.1, Q9.1, R13.2, R44.2, S2.2, S5.2
unnamed: Q4.3 (D), Q10.3 (D), R18.2, R19.1, R49.2, R50.1
unnamed: Q5.1, Q11.1, R21.2, R31.2, R52.2, R62.2
unnamed: Q6.1, Q12.1, R22.2, R30.2, R53.2, R61.2
unnamed: R2.1, R33.1, S3.1, S3.2, S6.1, S6.2
unnamed: R5.1, R36.1, U1.4 (A5_CC1), U4.4 (A5_CC1)
unnamed: R6.1, R37.1, U1.10 (B5_CC2), U4.10 (B5_CC2)
Nichrome: IC1.18 (GPIO15), IC13.18 (GPIO15), R1.1, R32.1
RUN: IC1.26 (RUN), IC13.26 (RUN), S1.1, S1.2, S4.1, S4.2
SWCLK: IC1.24 (SWCLK), IC13.24 (SWCLK), J1.1, J20.1
SWDIO: IC1.25 (SWDIO), IC13.25 (SWDIO), J1.3, J20.3
ToF_VCC: IC1.6 (GPIO4), IC13.6 (GPIO4), R31.1, R62.1
VBUS: D3.2 (A), D6.2 (A), Q2.1, Q8.1, U1.2 (A4-B9_VBUS), U1.11 (A9-B4_VBUS), U4.2 (A4-B9_VBUS), U4.11 (A9-B4_VBUS)
Vmonitor: IC1.39 (GPIO27/ADC1), IC13.39 (GPIO27/ADC1), Q4.2 (S), Q10.2 (S)
XIN: C3.2, C33.2, IC1.20 (XIN), IC13.20 (XIN), Y1.3, Y3.3
XOUT: IC1.21 (XOUT), IC13.21 (XOUT), R3.2, R34.2

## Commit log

2023-03-19 add major parts
    [kaguya-elec.kicad_sch]
2023-03-19 add pcb
    [kaguya-elec.kicad_pcb, kaguya-elec.kicad_sch]
2023-03-21 update pcb
    [kaguya-elec.kicad_pcb, kaguya-elec.kicad_sch]
2023-03-21 improve artwork
    [kaguya-elec.kicad_pcb, kaguya-elec.kicad_sch]
2023-03-26 em-1 done
    [kaguya-elec-B_Cu.gbr, kaguya-elec-B_Mask.gbr, kaguya-elec-B_Paste.gbr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]
2023-03-27 remove blind vias
    [kaguya-elec-B_Cu.gbr, kaguya-elec-B_Mask.gbr, kaguya-elec-B_Paste.gbr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]
2023-04-06 fix erattas on em-1
    [kaguya-elec.kicad_pcb, kaguya-elec.kicad_sch]
2023-07-06 final ver
    [kaguya-elec-B_Cu.gbr, kaguya-elec-B_Mask.gbr, kaguya-elec-B_Paste.gbr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]
